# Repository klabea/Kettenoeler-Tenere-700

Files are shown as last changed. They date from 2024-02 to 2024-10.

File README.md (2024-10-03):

# Kettenöler Tenere 700
## Halter Scottoiler
Eine 3D-gedruckte Aufnahme für das Scottoiler vSystem. Die Aufnahme wird an einem Halter, der formschlüssig in der hinteren Freimachung der linken Motorstütze sitzt, verschraubt.

|Anzahl|Bezeichnung |Maße |DIN/EN |Bemerkung  |
|:---: | --- | --- | --- | --- |
|1 |Scottoiler, vSystem | | |Louis Edition  |
|1 |Bracket Scottoiler | | |PETG  |
|1 |Bracket Nut | | |PETG  |
|2 |Zylinderschraube mit Innensechskant|M5 x 25  |ISO 4762 | |
|2 |Sechskantmutter mit Klemmteil |M5 |DIN 6924 | | 
|2 |Scheibe |M5 | | |  

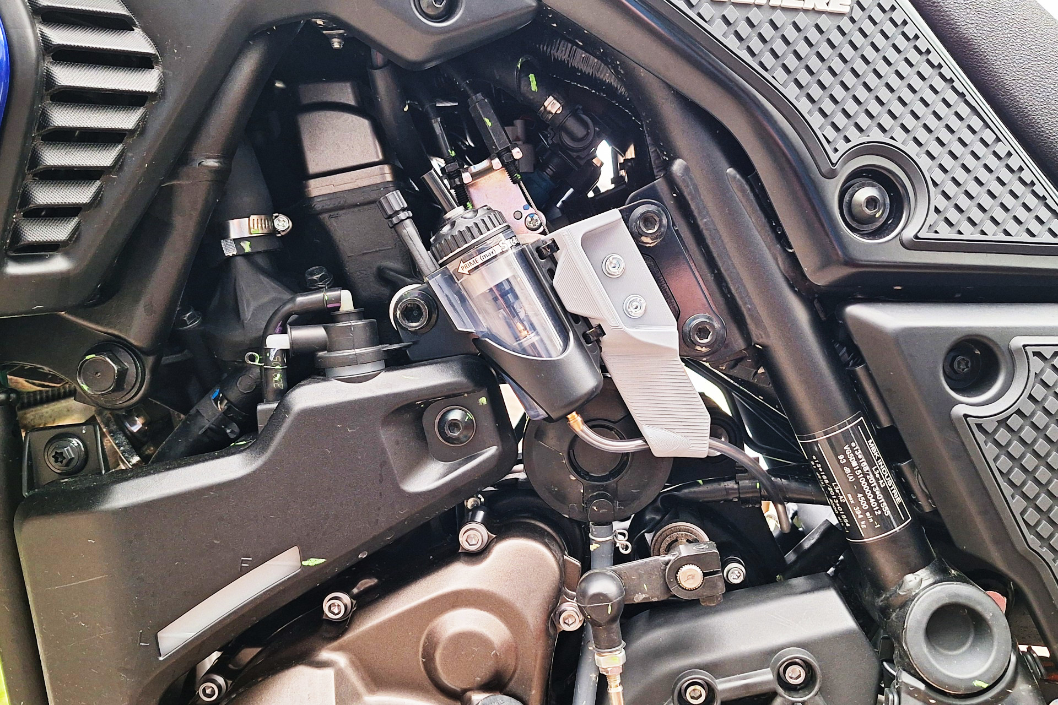
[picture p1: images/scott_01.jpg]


## Ritzelabdeckung
Eine 3D-gedruckte Abdeckung mit integrierter Schmiermittelzufuhr, ersetzt die originale OEM-Blende. Das Schmiermittel wird auf die ablaufende Kette, unten mittig, ca. 7 mm vom Ritzel (15Z) und ca. 16 mm zur Kette aufgeträufelt. Im voll eingefederten Zustand beträgt der Abstand zur Kette ca. 5 mm.

Die Tropfenbildung  kann gut über die Freimachungen in der Abdeckung beobachtet werden.

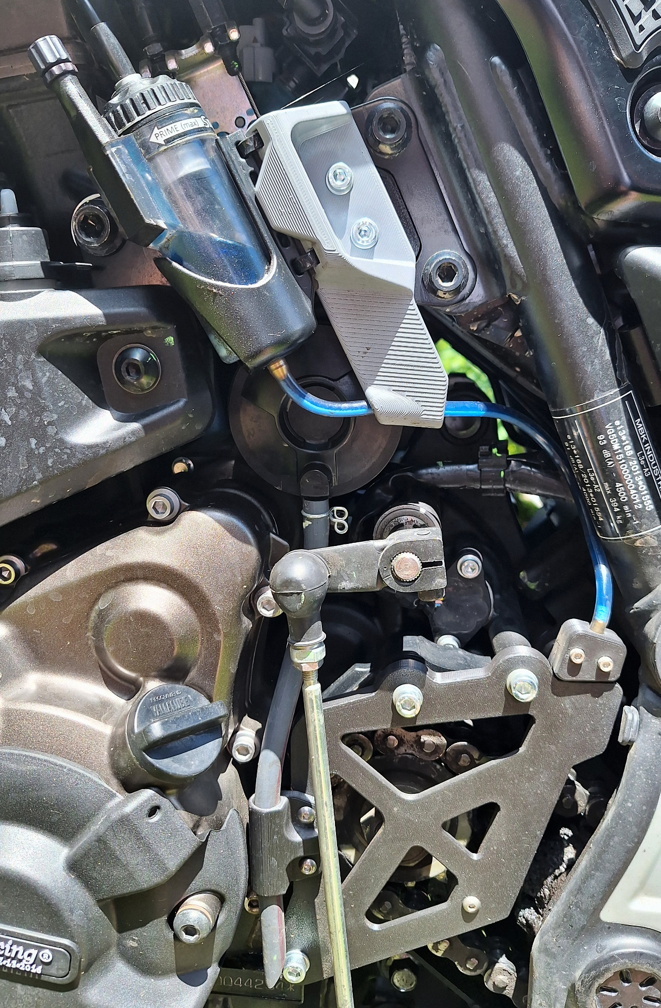
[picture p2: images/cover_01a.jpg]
Cover


|Pos.  |Anzahl|Bezeichnung |Maße |DIN/EN |Bemerkung  |
|:---: |:---:  | --- | --- | --- | --- |
|1 |1 |Cover | | |PETG / ASA  |
|2 |1 |Guide Tube | | |PETG / ASA  |
|3 |1 |Clamp outboard | | |PETG / ASA  |
|4 |1 |Clamp inboard | | |PETG / ASA  |
|5 |1 |Bracket Hose | | |PETG / ASA  |
|6 |1 |Rohr |3 x 1,6  | |CuZn |
|7 |2 |Gewindeeinsatz |M3 | | |
|8 |3 |Gewindeeinsatz |M4 | | |
|9 |3 |Distanzhülse |10 x 6,6 x 15  | |Al | 
|10 |2 |Zylinderschraube mit Innensechskant  |M3 x 10  |ISO 4762 | |
|11 |3 |Flachrundkopfschraube mit Innensechskant|M4 x 10  |ISO 7380-1 | |
|12 |3 |Scheibe |M4 | | |

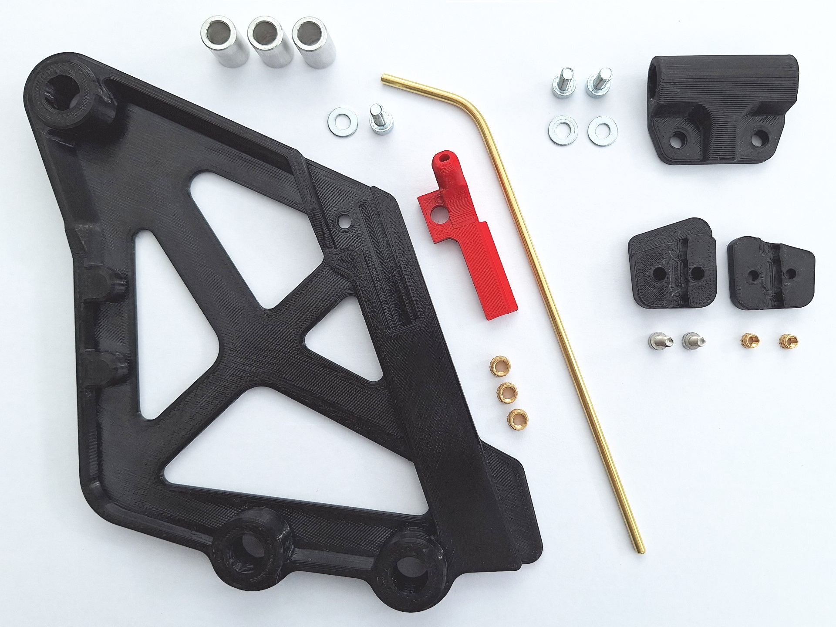
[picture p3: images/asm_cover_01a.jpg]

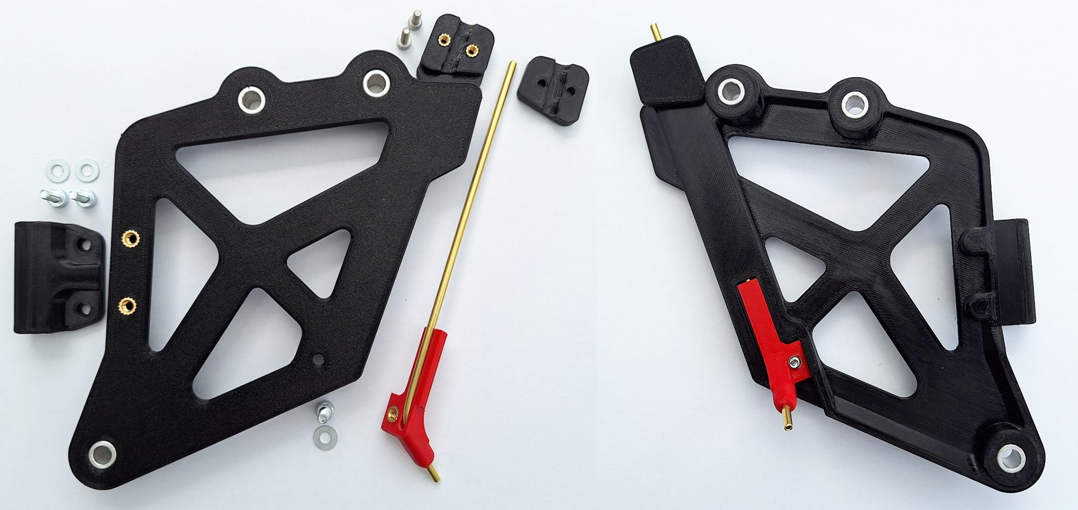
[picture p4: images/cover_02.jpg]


Befestigung der Ritzelabdeckung: Tausch der OEM-Schraube M6 x 20 erforderlich (Schraubenüberstand original 12 mm)
|Pos.  |Anzahl|Bezeichnung |Maße |DIN/EN |Bemerkung  |
|:---: |:---:  | --- | --- | --- | --- |
|1 |3 |Zylinderschraube mit Innensechskant  |M6 x 30  |ISO 4762 |evt. 2mm kürzen  |
|2 |3 |Scheibe |M6 | | |

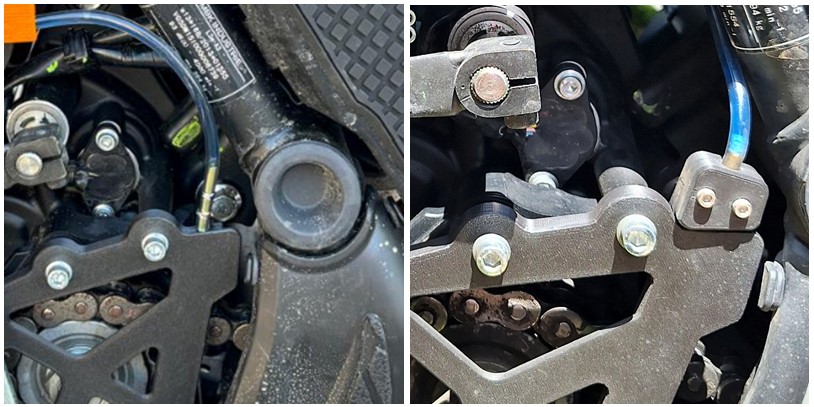
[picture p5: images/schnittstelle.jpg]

Schlauchbefestigung mittels Draht oder Klemmschellen

### Info
- **Muttern statt Gewindeeinsätze:** die Dateien mit der Namensendung "_nut" sind für Seckskantmuttern ausgelegt.
- **Variante 2mm:** Ausgelegt für ein CuZn-Rohr mit einem Außendurchmesser von 2 mm.

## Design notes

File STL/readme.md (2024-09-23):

# Angaben für PrusaSlicer
## Halter Scottoiler

**Bracket Nut:**
* PETG
* Nozzel 0,4 mm
* Schichthöhe 0,2 mm
* Perimeter 3
* Infill 50%
* auf den Achsen der M5-Verschraubungen Modifizierer, Zylinder ø12 mm, hinzugefügt: Infill 100%
* Stützen: Stützen nur auf dem Druckbett

**Bracket Scottoiler:**
* PETG
* Nozzel 0,4 mm
* Schichthöhe 0,2 mm
* Perimeter 3
* Infill 50%
* auf den Achsen der M5-Verschraubungen Modifizierer, Zylinder ø12 mm, hinzugefügt: Infill 100%
* Stützen: Stützen nur auf dem Druckbett (Organisch)

## Ritzelabdeckung

**Cover:**
* PETG / ASA
* Nozzel 0,4 mm
* Schichthöhe 0,2 mm
* Perimeter 3
* Infill 30%
* Cover Nut: auf den Achsen der M4-Verschraubungen Modifizierer, Zylinder ø12 mm, hinzugefügt: Infill 100%

**Bracket Hose:**
* PETG / ASA
* Nozzel 0,4 mm
* Schichthöhe 0,2 mm
* Perimeter 3
* Infill 30%
* auf den Achsen der M4-Verschraubungen Modifizierer, Zylinder ø12 mm, hinzugefügt: Infill 100%

**Guide Tube und Clamp IB/OB:**
* PETG / ASA
* Nozzel 0,4 mm
* Schichthöhe 0,2 mm
* Infill 100%

## UPDATE 2024-09-23
* **Cover-02:** Untere Schraubenaufnahme um 1 mm versetzt, Versteifungen hinzu.
* **Cover-02 (2mm):** Untere Schraubenaufnahme um 1 mm versetzt, Versteifungen u. Schlauchführung ø4,1 hinzu.

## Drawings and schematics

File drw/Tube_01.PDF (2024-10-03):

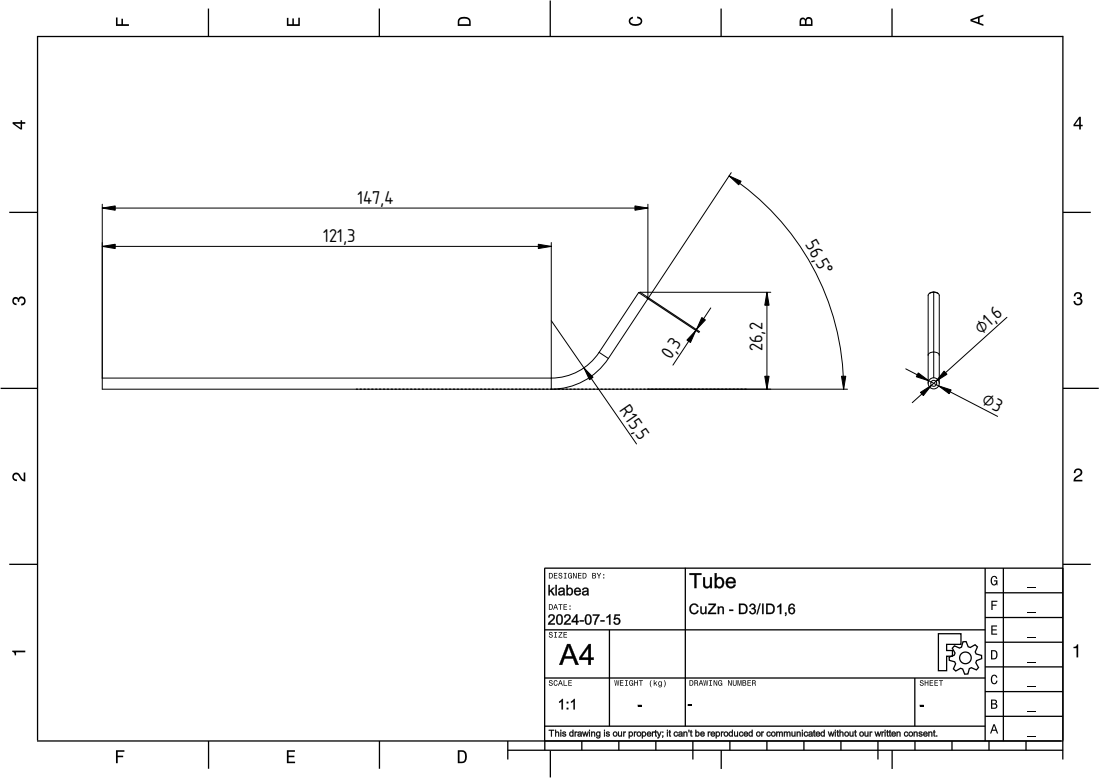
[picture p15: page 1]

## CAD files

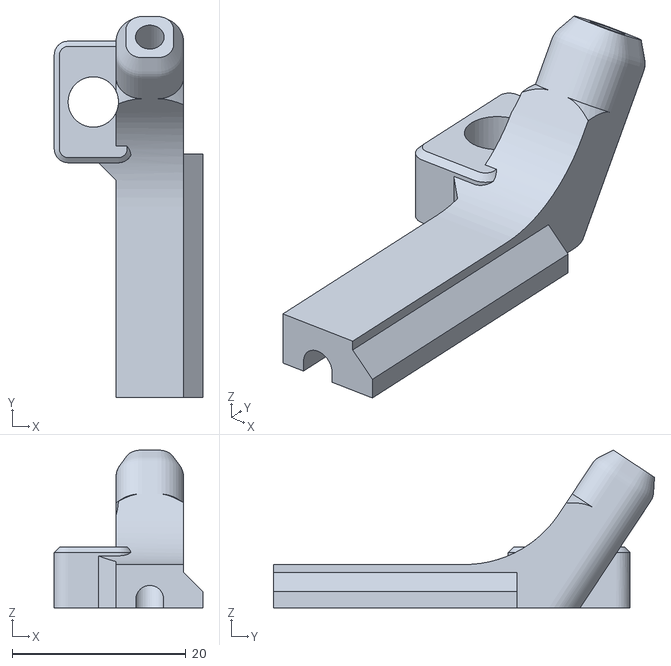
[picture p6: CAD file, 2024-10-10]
STL/guide-tube_01_fix5.stl
17.1 x 43.8 x 18.2

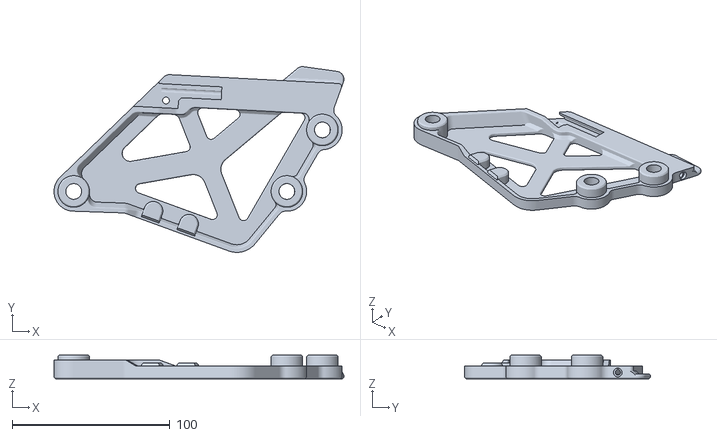
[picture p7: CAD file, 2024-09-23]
STL/cover_02.stl
183.7 x 117.7 x 15.0

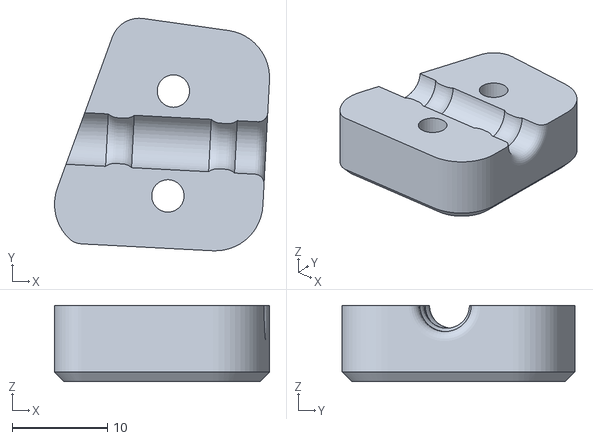
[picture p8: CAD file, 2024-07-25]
STL/clamp_outboard_01.stl
22.5 x 24.4 x 8.00

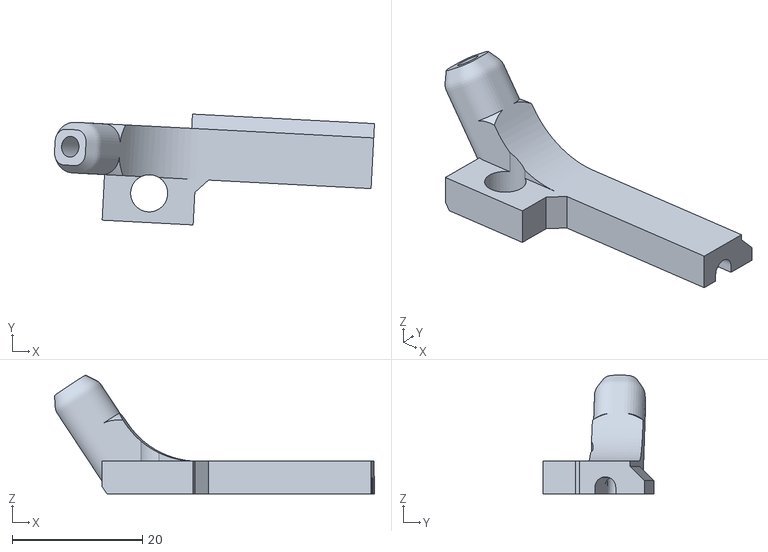
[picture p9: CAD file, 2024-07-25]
STL/guide_tube_01.stl
49.1 x 17.0 x 18.2

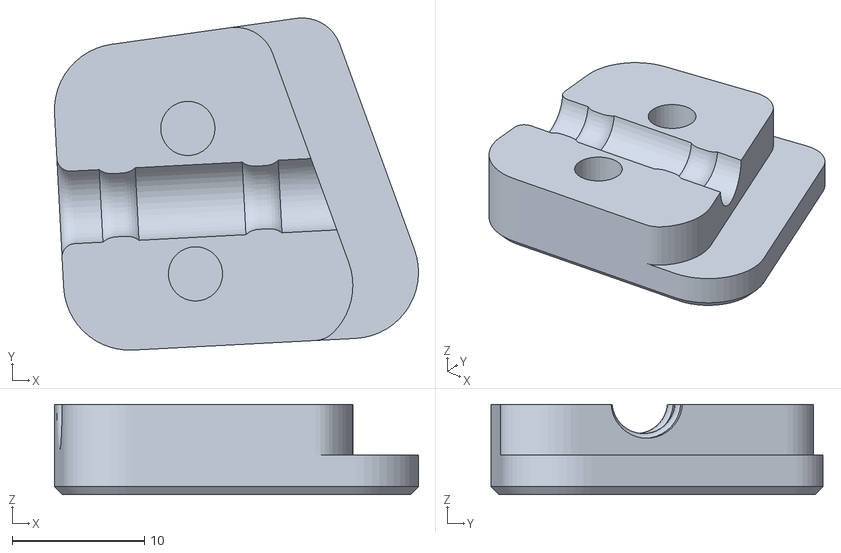
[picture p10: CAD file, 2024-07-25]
STL/clamp_inboard_01.stl
27.5 x 25.1 x 6.80

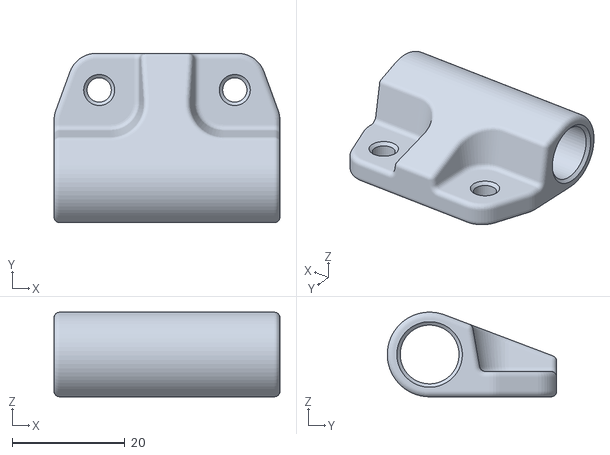
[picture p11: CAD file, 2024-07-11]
STL/bracket_hose_01.stl
40.0 x 30.0 x 15.0

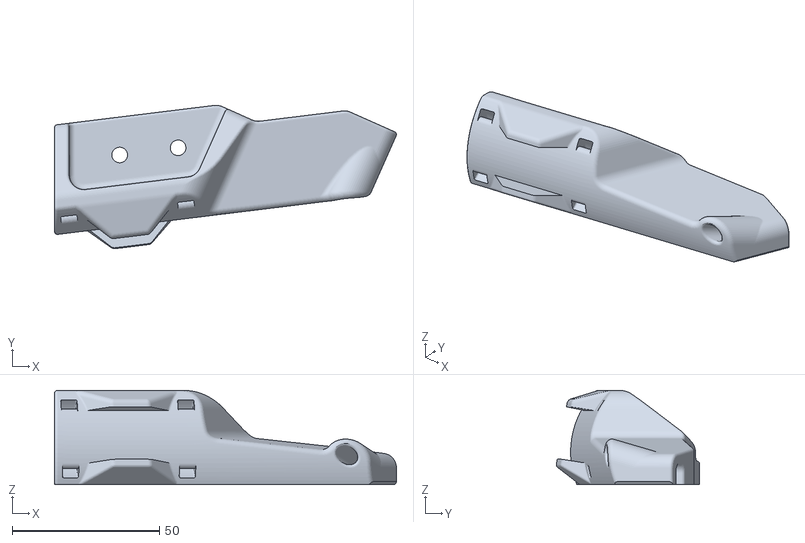
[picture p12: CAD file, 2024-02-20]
STL/bracket_scottoiler_01.stl
116.1 x 48.7 x 32.0

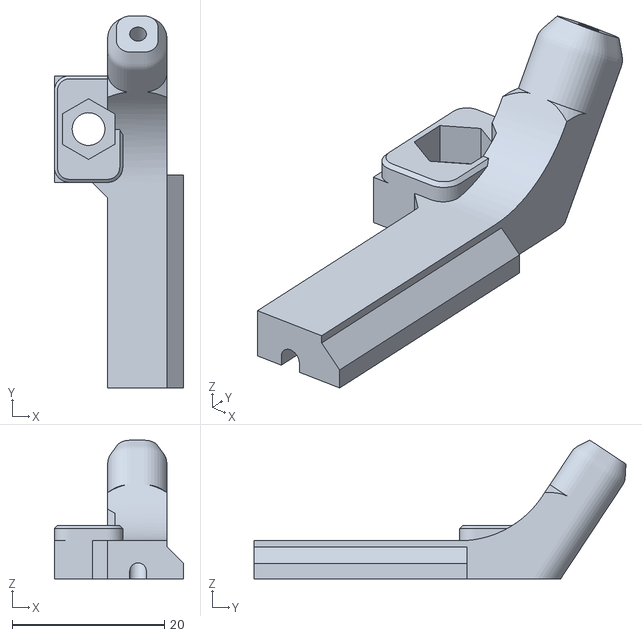
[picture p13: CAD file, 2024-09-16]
STL/2mm/guide_tube_01_nut_2mm.stl
17.0 x 48.8 x 18.2

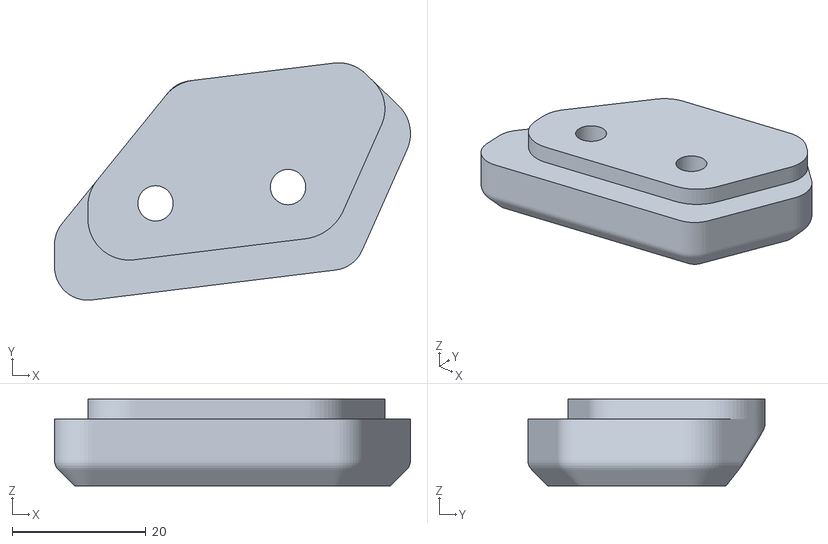
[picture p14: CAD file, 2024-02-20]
STL/bracket_nut_01.stl
53.3 x 35.6 x 13.0

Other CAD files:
STL/2mm/guide-tube_01_fix5_nut_2mm.stl
STL/2mm/cover_02_nut_2mm.stl
STL/guide-tube_01_fix5_nut.stl
STL/cover_02_nut.stl
STL/clamp_inboard_01_nut.stl
STL/guide_tube_01_nut.stl
